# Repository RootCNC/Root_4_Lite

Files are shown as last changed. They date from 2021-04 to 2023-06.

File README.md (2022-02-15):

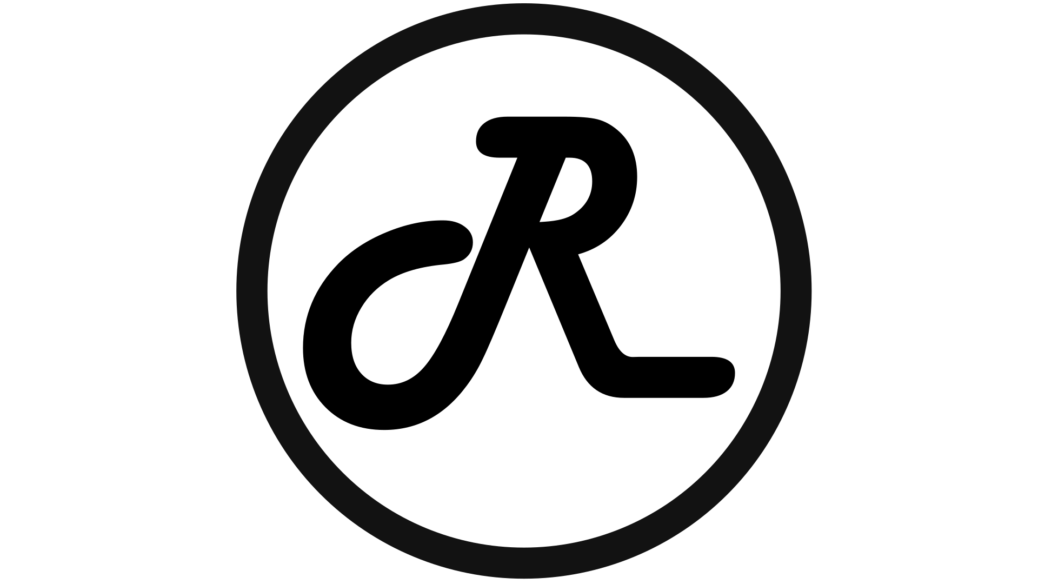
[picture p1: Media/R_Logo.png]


# Root 4 LITE CNC - High Performance small scale 3D Printed CNC Machine 

Root 4 Lite is deisgned to be a **low cost high performance CNC machine** that anyone can make at home.

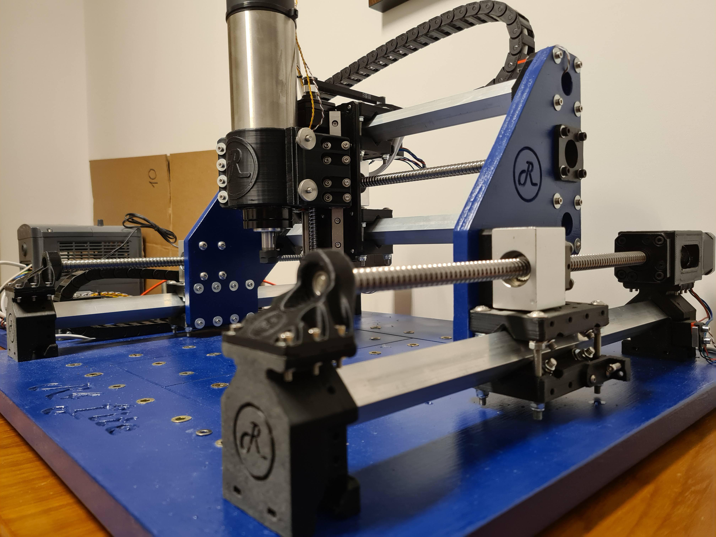
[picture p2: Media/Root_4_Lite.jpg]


### Goals
- Low Cost (Under £500)
- All bal screw design for percision movement
- Support for High performance VFD spindles
- Use low Cost NEMA17 Stepper motors
- Standard off the shelf parts
- Easily sourced components
- 3D printable
- Scaleable

## Spec
- Working Area = 224*280*60mm (Z,Y,Z) - Default build for other diemensions please see [LINK](https://github.com/RootCNC/Root_4_Lite/blob/main/Working%20Area.xlsx)
- Stepper Motor = NEMA 17 
- Aux rails for mounting a laser or dust shoe
- All ballscrew design
- Linear guide Z Axis
- Driect Drive Motors
- Full VFD support

## Videos

Youtube Videos can be found [Here](https://www.youtube.com/sailorpete12)

### Detailed build Videos

(http://www.youtube.com/watch?v=DjvXqU2bEzY "")

(http://www.youtube.com/watch?v=-5PmiW85Cyw "")

(http://www.youtube.com/watch?v=_y3V89cwmr8 "")

## License

This project is licensed under the Creative Commons 4.0 license with 
Attribution-NonCommerial-ShareAlike see `LICENSE.txt` for details

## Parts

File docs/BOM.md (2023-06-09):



# 3D Printed Parts required

|	3D Printed Parts  	|	Required	|	QTY	|	Total Weight (g)	|
|	---	|	---	|	---	|	---	|
|	Y_Axis_BoxMount.STL	|	4	|	YES	|	232g	|
|	Z_Y_Axis_BallscrewSpacer.STL	|	3	|	YES	|	39g	|
|	X_Axis_MotorMount.STL	|	1	|	YES	|	30g	|
|	X_Y_Axis_Carriage.STL	|	8	|	YES	|	344g	|
|	X_Axis_BearingIdler.STL	|	1	|	YES	|	17g	|
|	Y_Axis_Idler.STL	|	2	|	YES	|	28g	|
|	Z_Axis_Carriage_65mm.STL	|	1	|	YES	|	200g	|
|	Z_Axis_LinearRailMount.STL	|	1	|	YES	|	110g	|
|	Y_Aixs_DragChainMount.STL	|	1	|	YES	|	20g	|
|	X_Aixs_DragChainMount.STL	|	1	|	YES	|	15g	|
|	Z_Axis_MotorMount.STL	|	1	|	YES	|	40g	|
|	Y_Axis_Foot.STL	|	4	|	YES	|	32g	|
|	X_Axis_BoxMount.STL	|	2	|	YES	|	138g	|
|	DustShoe_Bottom.STL	|	1	|	YES	|	46g	|
|	DustShoe_Rail_Right.STL	|	1	|	YES	|	17g	|
|	DustShoe_Rail_Left.STL	|	1	|	YES	|	17g	|
|	Y_Axis_Motor_FK10_BearingMount.STL	|	2	|	YES	|	70g	|
|	Y_Axis_Endstop_Spacer.STL	|	1	|	NO	|	0g	|
|	Y_Axis_AdjEndstop.STL	|	1	|	NO	|	0g	|
|		|		|		|	Filament Used = 1395g	|

# Panels
| Item | QTY | Link|
|---|---|-----|
|Side_Panel|2|[Root CNC Store](https://rootcnc.com/product/root-4-lite-side-panels/)|
|Baseboard |1|Comming Soon|

# Electronics/ Electro Mechanical
| Item | Required | QTY | Link|
|---|---|---|-----|
|Root CNC ESP32-GRBL Controller |Yes|1|[LINK](https://rootcnc.com/product/root-controller-rev-2-1/)|
|Root CNC Controller Motor breakout (non-isolated) used DVR8825 or similar driver (Buy an isolated stepper driver) |Yes|1|Obsolete|
|DRV8825 or similar stepper motor drivers|Yes|4|[LINK](https://s.click.aliexpress.com/e/_A3iYCN) [LINK](https://s.click.aliexpress.com/e/_97wkVB) [UK LINK](https://amzn.to/3yf2EHw)
| Nema 17 Bipolar 59Ncm (84oz.in) 2A | Yes | 4 | [LINK](https://www.omc-stepperonline.com/nema-17-bipolar-59ncm-84oz-in-2a-42x48mm-4-wires-w-1m-cable-connector-17hs19-2004s1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) [LINK](https://www.omc-stepperonline.com/5pcs-of-nema-17-bipolaire-59ncm-84oz-in-2a-42x48mm-4-fils-w-1m-cable-connector-5-17hs19-2004s1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)
|1.5KW Spindle with VFD|Yes|1|[LINK_1](https://s.click.aliexpress.com/e/_dX0JKm3) [LINK_2](https://s.click.aliexpress.com/e/_dT4xs63) [LINK_3](https://s.click.aliexpress.com/e/_dSjt6gr) [LINK_4](https://s.click.aliexpress.com/e/_dSUhh43)
|Micro Switch SPDT micro switch V4 KW11i|Yes|6|[LINK UK](https://amzn.to/31Kf1wC) [LINK](https://s.click.aliexpress.com/e/_ATnQCz)| 
|12V or 24V PSU (For Controller power + any lights) |Yes|1|[12V_LINK_UK](https://amzn.to/2HxYvIS) [12V_lINK](https://s.click.aliexpress.com/e/_AACYyd)| 

# Motion
| Item | Required | QTY | Link|
|---|---|---|-----|
|608 Bearings | Yes | 4 |[LINK_UK](https://amzn.to/3dWB9c6), [LINK](https://s.click.aliexpress.com/e/_ATuujF)|
|625 Bearings | Yes | 38 |[LINK](https://s.click.aliexpress.com/e/_9iRVbr),  [LINK](https://s.click.aliexpress.com/e/_Ac5QYN),  [UK LINK](https://amzn.to/33OCsFN)|
|MGN12 150mm + (MGN12C x2) | Yes | 2 |[LINK](https://s.click.aliexpress.com/e/_A4Rr41)|
|GT2 Pulley 5mm Bore (16T) | Yes | 1 |[LINK](https://s.click.aliexpress.com/e/_9wTL2N),  [LINK](https://s.click.aliexpress.com/e/_9hLamt), [UK LINK](https://amzn.to/3waEtbq)|
|GT2 Pulley 8mm Bore (20T) | Yes | 1 |[LINK](https://s.click.aliexpress.com/e/_9wTL2N) |
|GT2 Closed loop belt (252 mm) | Yes |  1 ||
|Lead Screw 1204 400mm Long SFU1204 | Yes | 3 |[LINK](https://s.click.aliexpress.com/e/_9jDD3X),  [UK LINK](https://amzn.to/3eQJNLg)|
|Lead Screw 1204 200mm Long SFU1204 | Yes | 1 |[LINK](https://s.click.aliexpress.com/e/_Akbvnn), [UK LINK](https://amzn.to/3olI2sE)|
|Lead Screw ball nut Housing/Mount  SFU1204 | Yes |  3 |[LINK](https://s.click.aliexpress.com/e/_Ak3HhT), [UK LINK](https://amzn.to/3whPGqP)|
|FK10 Bearing Block | Yes |  4 |[LINK](https://s.click.aliexpress.com/e/_9RmTwd)|
|5mm to 8mm coupler | Yes | 3 |[LINK](https://s.click.aliexpress.com/e/_9AhiTb)  [UK LINK](https://amzn.to/3bwfNC8)|
|Drag Chain 10x20mm internal - 50cm | Yes |  2 |[LINK](https://s.click.aliexpress.com/e/_9wV1qz),  [UK LINK](https://amzn.to/3eURTm5)|

# Hardware
Below is guide on the QTY required/ the pack sizes I brought to assemble the Root 4 LITE CNC. I used Aluminium box section but steel would work just fine.
| Item | Required | QTY | Link|
|---|---|---|-----|
|20mm box section 410mm (scalable)|Yes|2||
|20mm box section 360mm (scalable)|Yes|2||

# Fixing List

|	Fixing list	|	Required	|	QTY	|
|	-----	|	-----	|	-----|
|	M3 PAN HEAD 20MM BOLT	|	Yes	|	30 (*1)	|
|	M3 PAN HEAD 25MM BOLT	|	Yes	|	30 (*1)	|
|	M3 PAN HEAD 30MM BOLT	|	Yes	|	30 (*1)	|
|	M3 CAP HEAD  10MM BOLT	|	Yes	|	30 (*1)	|
|	M3 CAP HEAD  14MM BOLT	|	Yes	|	30 (*1)	|
|	M3 CAP HEAD  16MM BOLT	|	Yes	|	30 (*1)	|
|	M3 CAP HEAD  25MM BOLT	|	Yes	|	30 (*1)	|
|	M3 CAP HEAD  30MM BOLT	|	Yes	|	30 (*1)	|
|	M3 NUTS	|	Yes	|	100 (*1)	|
|	M3 STANDARD WASHER	|	Yes	|	30 (*1)	|
|	M3 PENNY WASHER	|	Yes	|	50 (*1)	|
|	M4 CAP HEAD 25MM BOLT	|	Yes	|	30 (*1)	|
|	M4 CAP HEAD 40MM BOLT	|	Yes	|	30 (*1)	|
|	M4 NUTS	|	Yes	|	50 (*1)	|
|	M4 STANDARD WASHERS	|	Yes	|	50 (*1)	|
|	M5 HEX HEAD 20MM BOLT	|	Yes	|	32	|
|	M5 PAN HEAD 20MM BOLT	|	Yes	|	20 (*1)	|
|	M5 PAN HEAD 30MM BOLT	|	Yes	|	20 (*1)	|
|	M5 PAN HEAD 60MM BOLT	|	Yes	|	16	|
|	M5 WASHERS	|	Yes	|	128	|
|	M5 NUTS	|	Yes	|	100 (*1)	|
|	M5 LOC NUTS	|	Yes	|	100  (*1)	|
|	M5 KNURLED THUMB NUTS 	|	Yes	|	4	|
|	M6 INSERTS NUTS	|	Yes	|	42	|

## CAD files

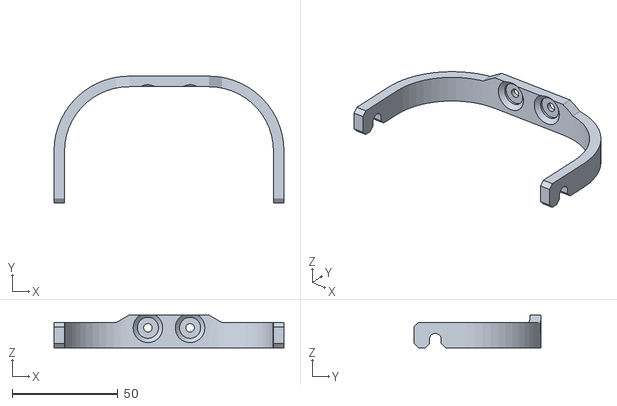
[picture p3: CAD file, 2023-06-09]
Addons/Laser Mount (LT-80W-AA)/Z_AxisMountBottom.stl
109.0 x 60.0 x 15.5

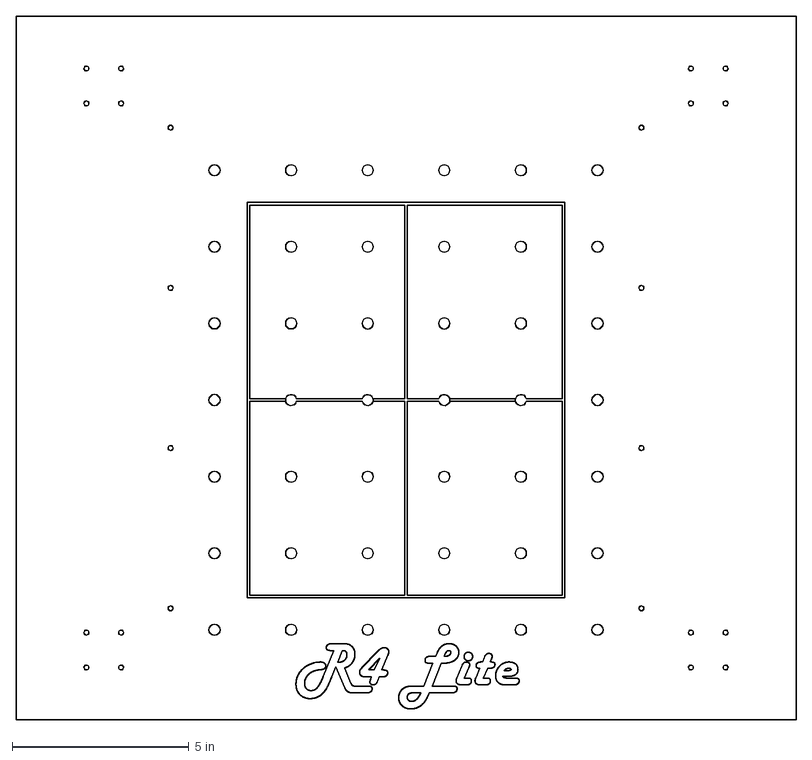
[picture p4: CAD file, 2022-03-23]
Source/DXF_Files/Root_4_Base_Board.dxf
22.0 x 19.9 in

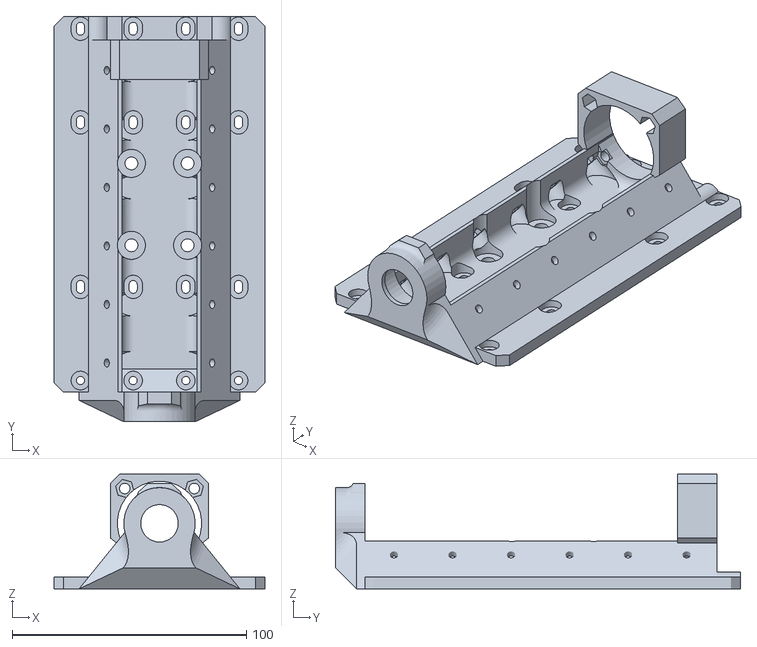
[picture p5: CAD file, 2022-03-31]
Source/STL_Files/Z_Axis_LinearRailMount.STL
90.0 x 173.0 x 49.0

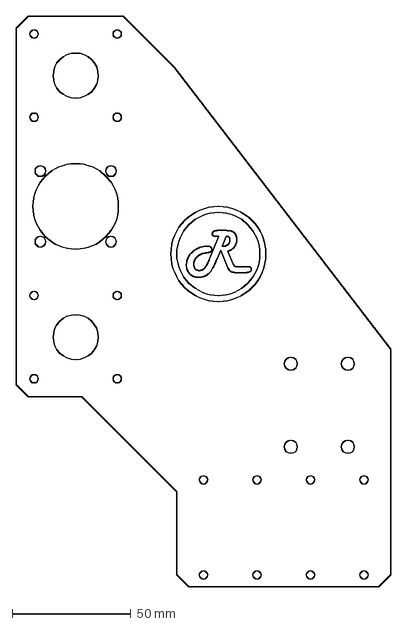
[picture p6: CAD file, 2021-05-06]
Source/DXF_Files/Root_4_Lite_Side_Panel_(Front).DXF
157.5 x 240.0 mm

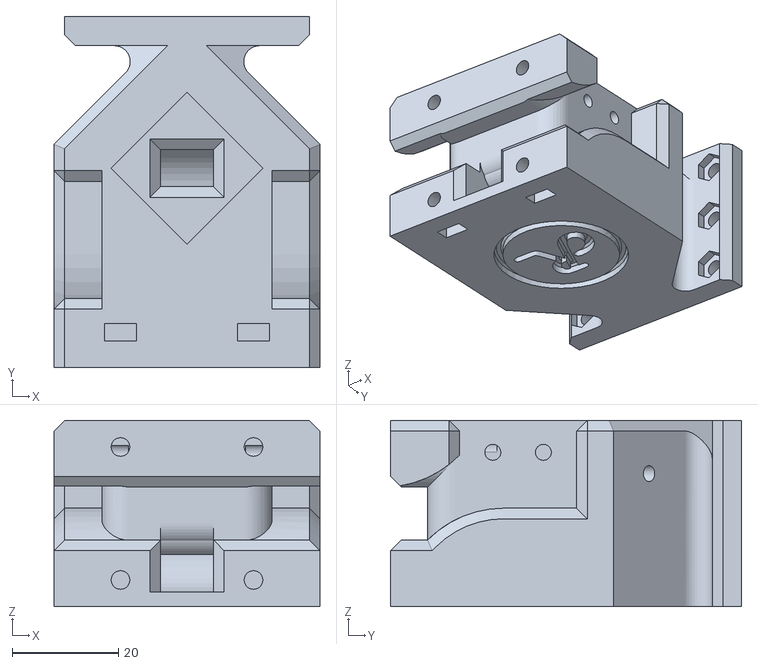
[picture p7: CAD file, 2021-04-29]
Source/STL_Files/Y_Axis_BoxMount.STL
50.0 x 66.0 x 35.0

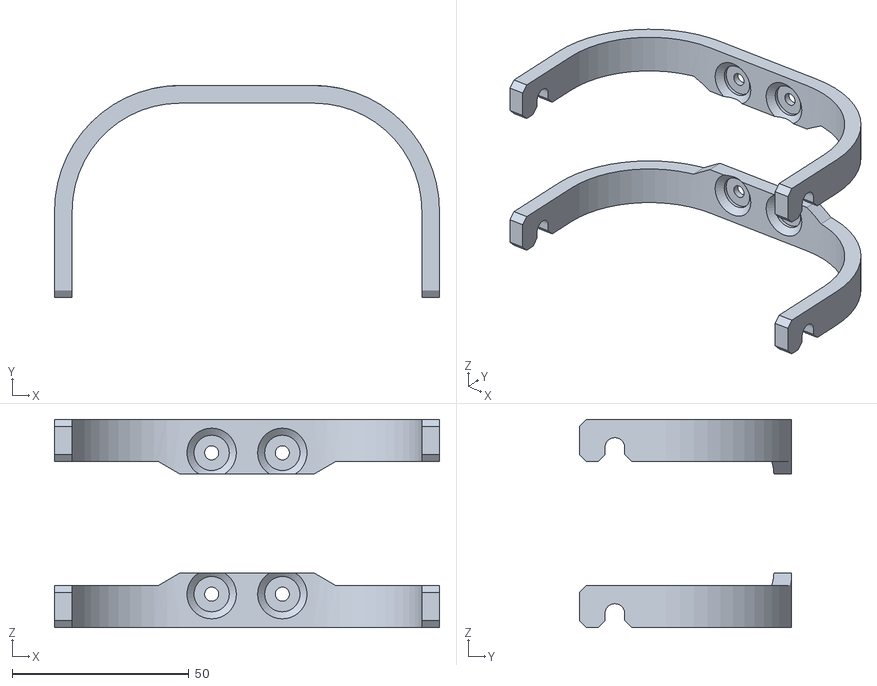
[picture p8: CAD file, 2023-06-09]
Addons/Laser Mount (LT-80W-AA)/Z_AxisMount.STL
109.0 x 60.0 x 59.0

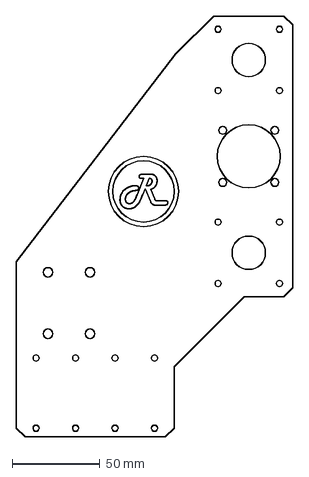
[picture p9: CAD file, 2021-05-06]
Source/DXF_Files/Root_4_Lite_Side_Panel_(Back).DXF
157.5 x 240.0 mm

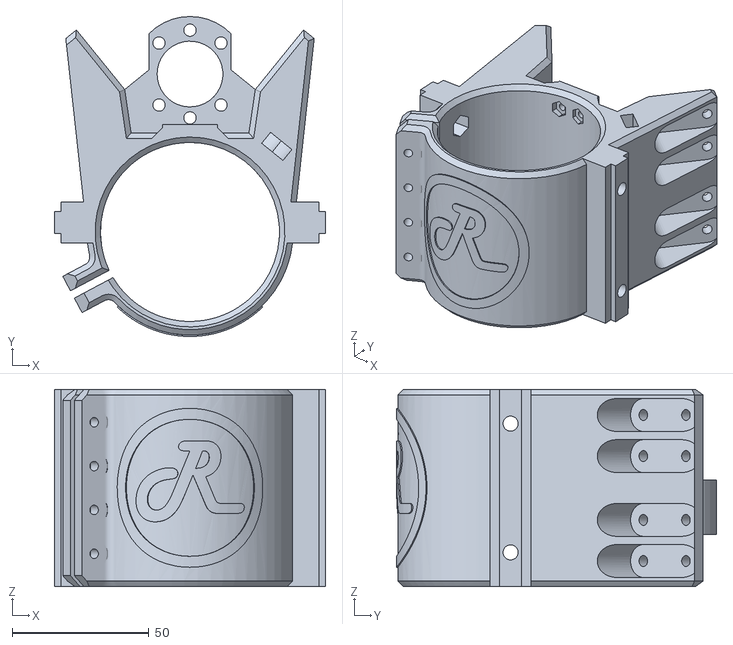
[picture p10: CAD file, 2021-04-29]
Source/STL_Files/Z_Axis_Carriage_65mm.STL
99.0 x 116.8 x 72.0

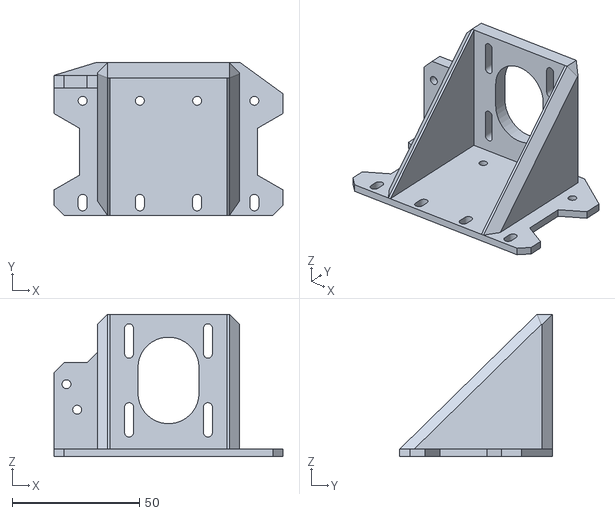
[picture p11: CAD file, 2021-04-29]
Source/STL_Files/Z_Axis_MotorMount.STL
90.0 x 60.0 x 56.0

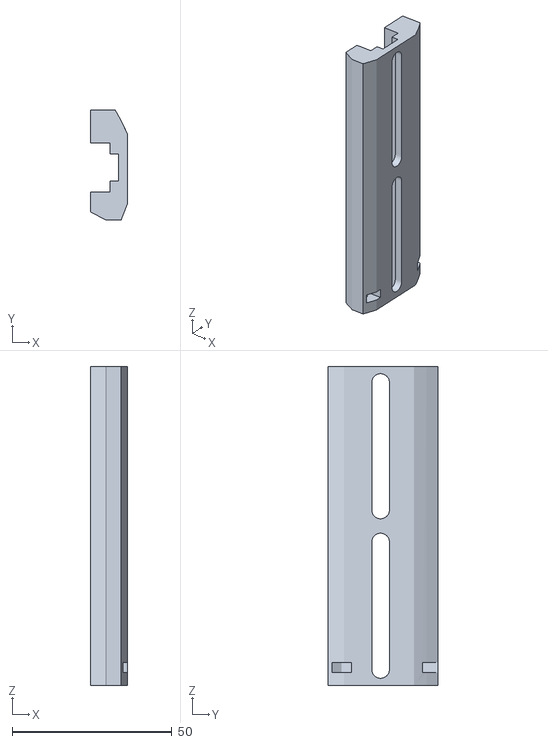
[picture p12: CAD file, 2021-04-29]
Source/STL_Files/DustShoe_Rail_Right.STL
11.5 x 34.5 x 100.0

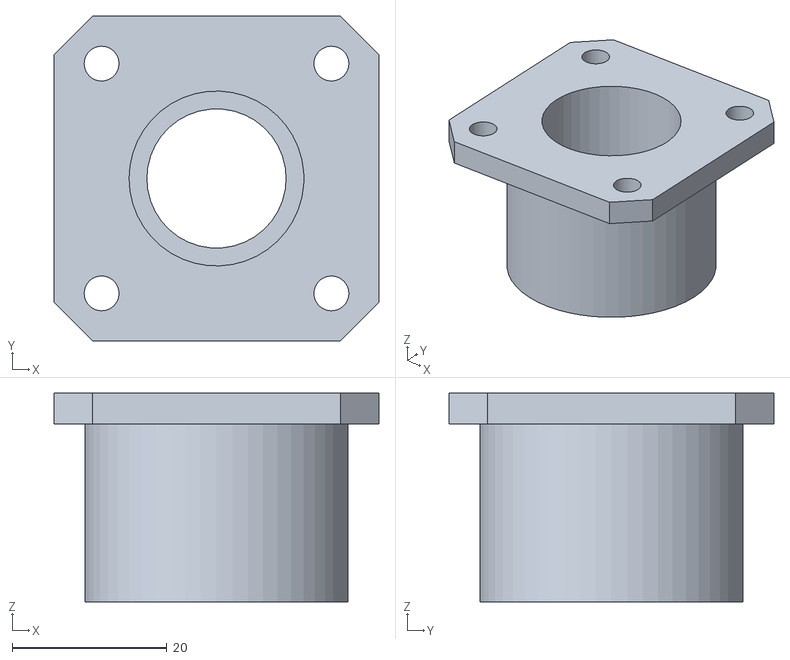
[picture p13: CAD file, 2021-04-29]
Source/STL_Files/X_Axis_BearingIdler.STL
42.0 x 42.0 x 27.0

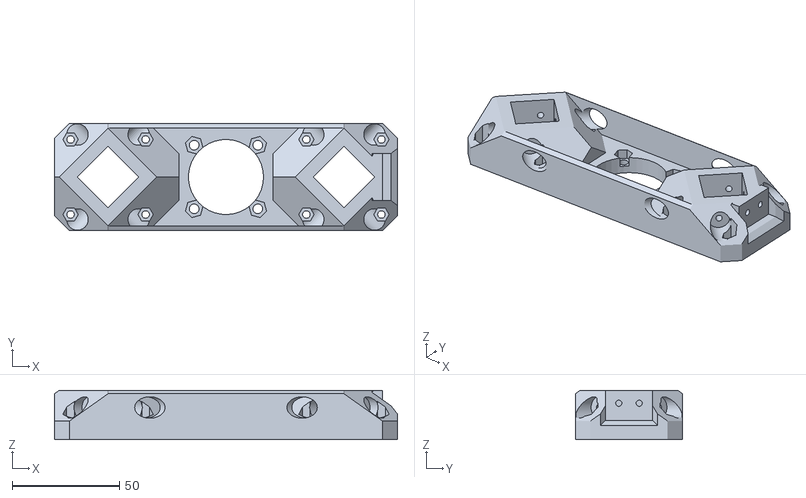
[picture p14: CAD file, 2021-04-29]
Source/STL_Files/X_Axis_BoxMount.STL
160.0 x 50.0 x 23.0

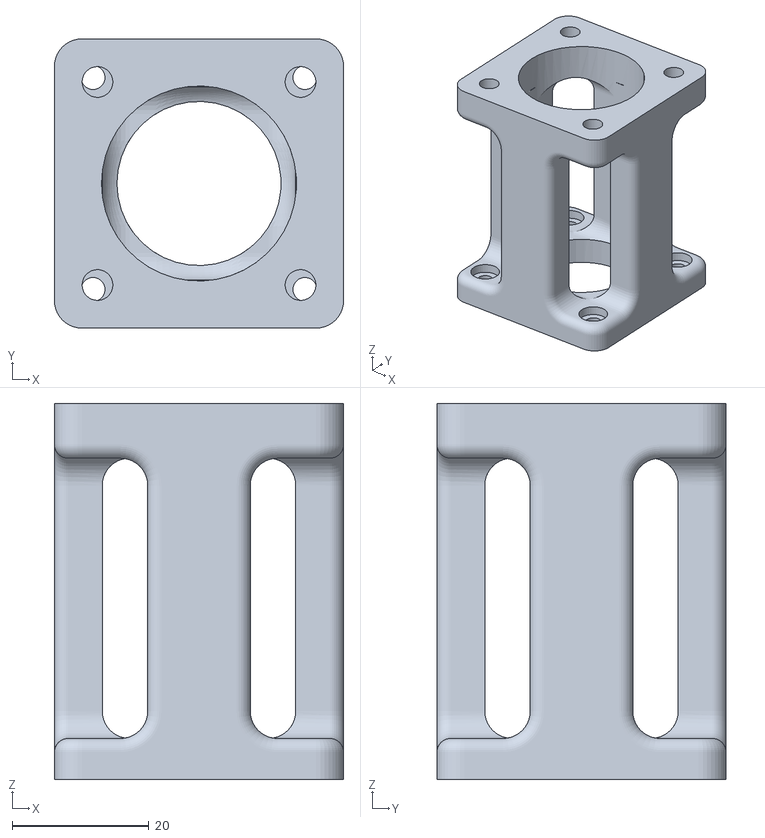
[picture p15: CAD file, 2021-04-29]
Source/STL_Files/X_Axis_MotorMount.STL
42.3 x 42.3 x 55.0

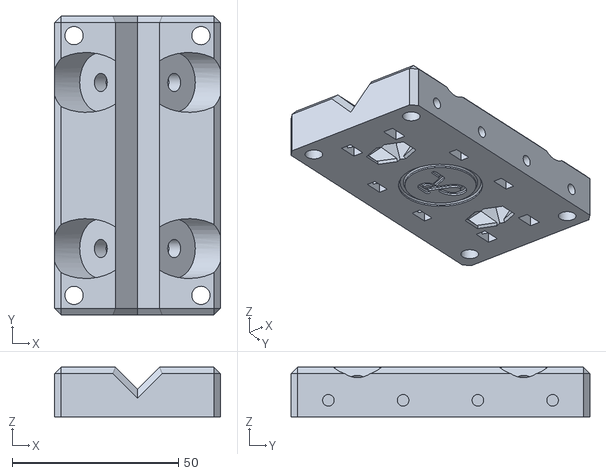
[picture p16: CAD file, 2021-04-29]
Source/STL_Files/X_Y_Axis_Carriage.STL
50.0 x 90.0 x 15.0

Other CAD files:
Addons/Laser Mount (LT-80W-AA)/Z_AxisMountTop.stl
Source/STL_Files/Y_Axis_Foot.STL
Source/STL_Files/Y_Axis_Idler.STL
Source/STL_Files/DustShoe_Bottom.STL
Source/STL_Files/X_Aixs_DragChainMount.STL
Source/STL_Files/Y_Aixs_DragChainMount.STL
Source/STL_Files/Y_Axis_AdjEndstop.STL
Source/STL_Files/Y_Axis_Endstop_Spacer.STL
Source/STL_Files/Y_Axis_Motor_FK10_BearingMount.STL
Source/STL_Files/Z_Y_Axis_BallscrewSpacer.STL

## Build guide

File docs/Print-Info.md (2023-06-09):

---
title: Root 4 Lite Print Orientation
description: How to print the parts for the Root 4 Lite
published: true
date: 2022-06-28T22:24:57.245Z
tags: root 4 lite, how to print
editor: markdown
dateCreated: 2022-06-28T22:17:17.168Z
---

# How to Print
Print settings for any of the Root CNC machine is key for a long lasting - high performance CNC machine. Below are the setting I used:

Resolution: 0.25-0.35mm
Infill: 50-60%
## Notes:
- Strength is key! use the hardest settings possible
- Print with 3-4 perimeters
- Print with ABS, PETG PLA will be fine though your mileage may vary (I am worried about the low glass transistion point of PLA being too low for the motors)

# DustShoe_Bottom.STL

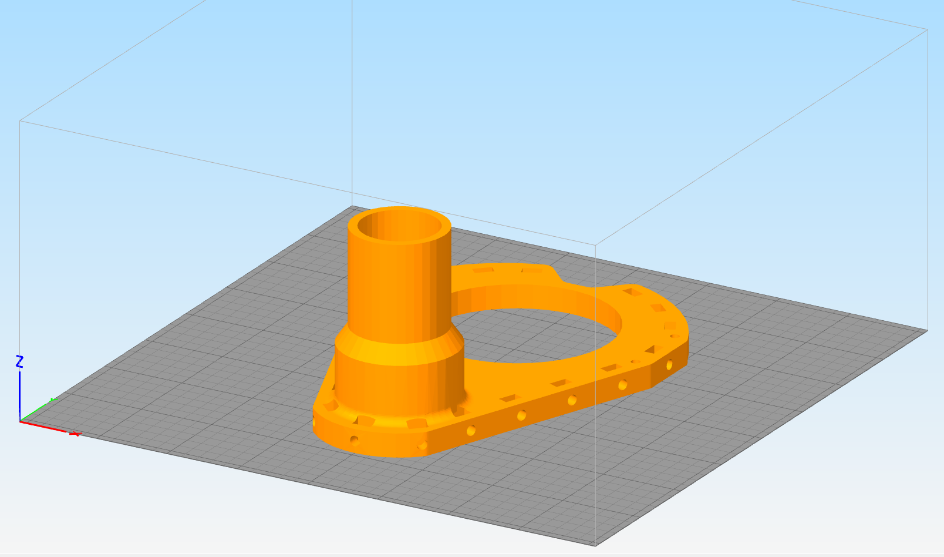
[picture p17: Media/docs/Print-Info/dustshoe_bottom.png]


# DustShoe_Rail_Right.STL

> For the left side - Please mirror in your slicer
{.is-info}

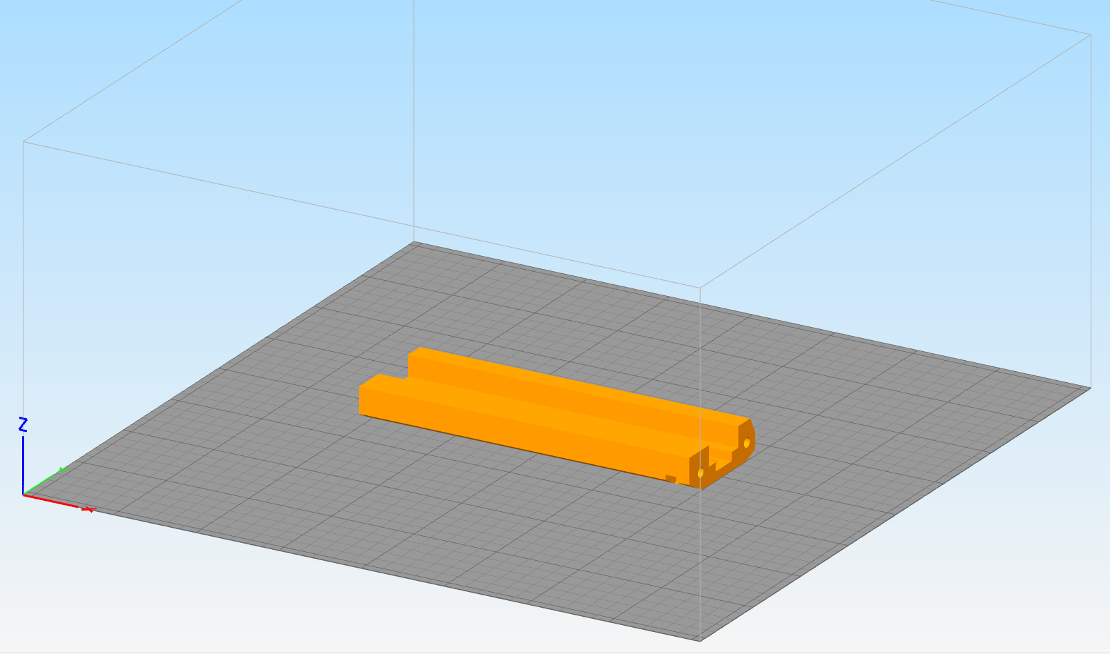
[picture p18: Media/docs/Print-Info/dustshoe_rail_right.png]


# X_Aixs_DragChainMount.STL.
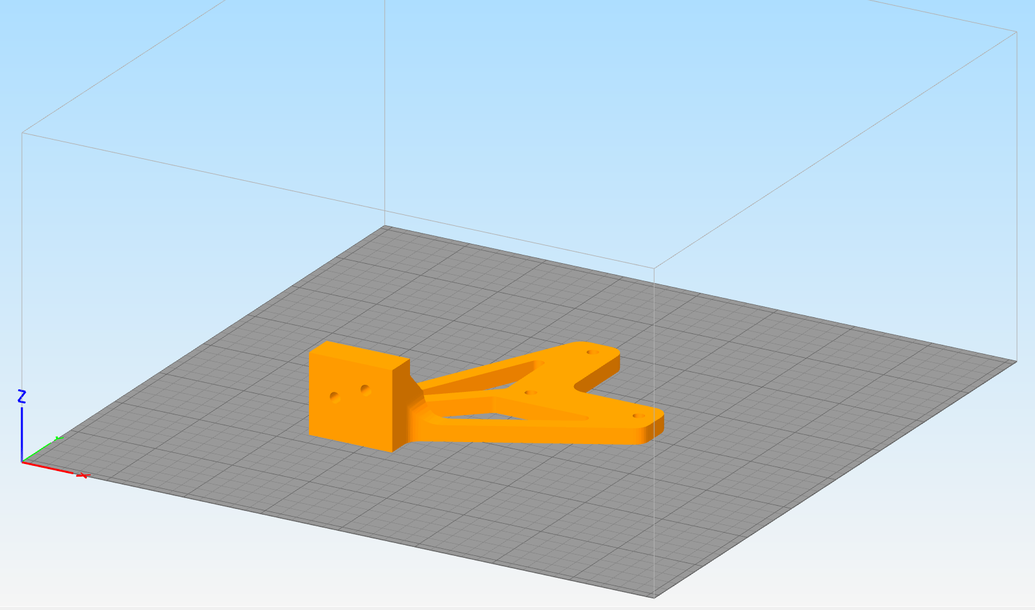
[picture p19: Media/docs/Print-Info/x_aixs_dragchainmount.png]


# X_Axis_BearingIdler.STL
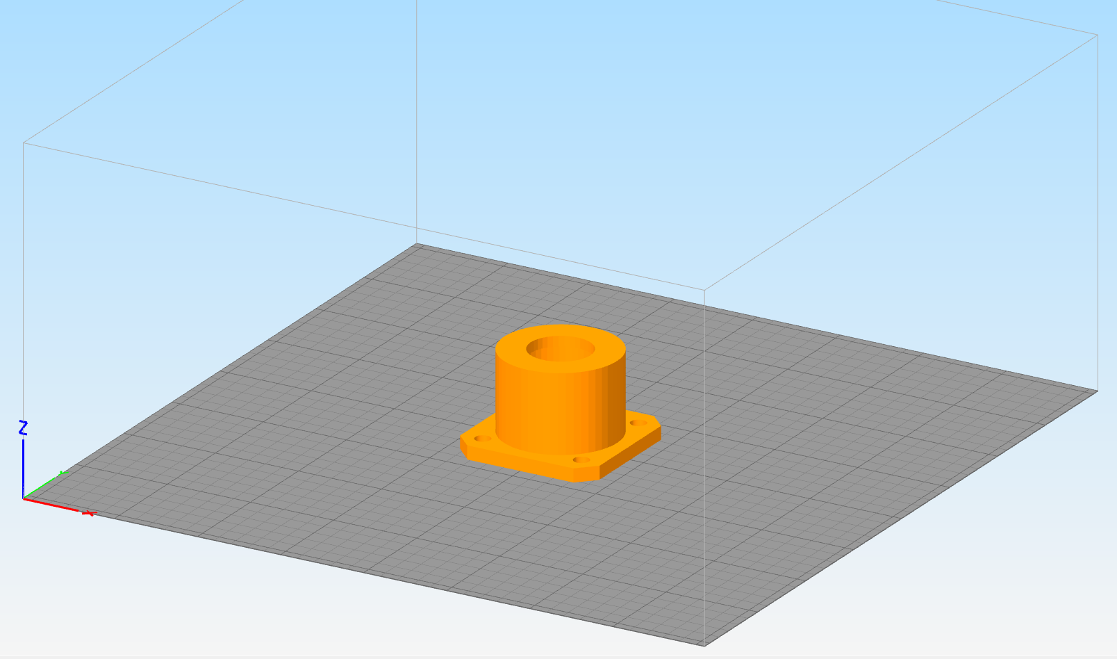
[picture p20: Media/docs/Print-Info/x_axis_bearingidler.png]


# X_Axis_BoxMount.STL
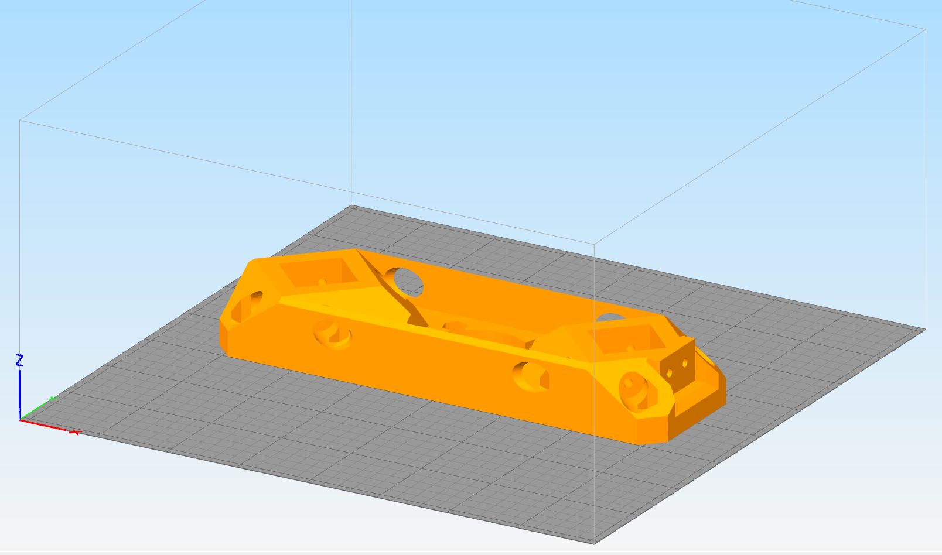
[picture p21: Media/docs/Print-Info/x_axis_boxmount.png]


# X_Axis_MotorMount.STL

> Needs supports, print with hex nut end down

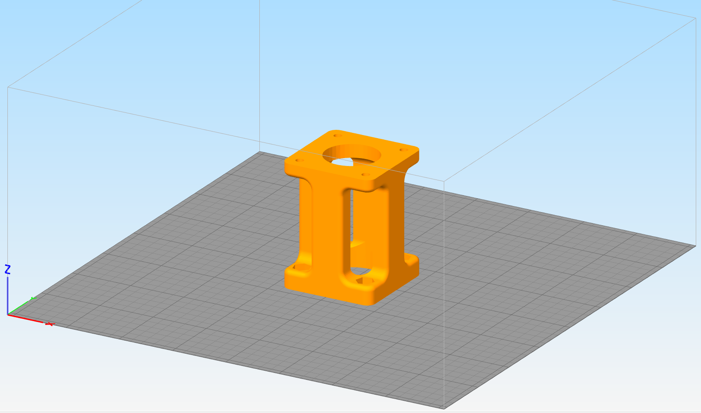
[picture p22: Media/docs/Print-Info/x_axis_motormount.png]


# X_Y_Axis_Carriage.STL
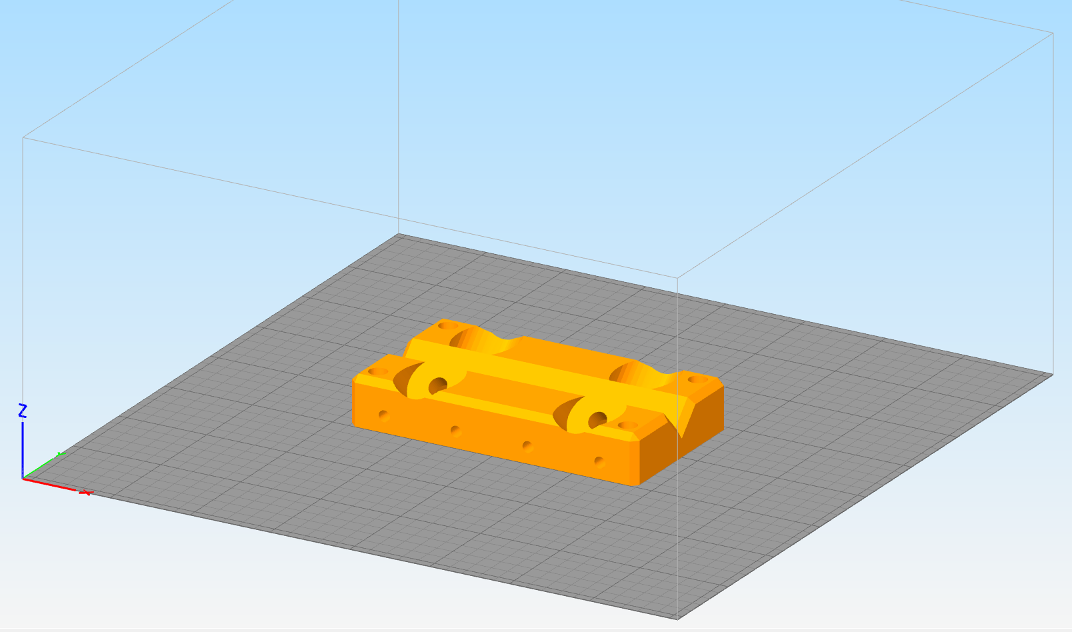
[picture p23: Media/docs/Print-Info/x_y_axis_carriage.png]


# Y_Aixs_DragChainMount.STL
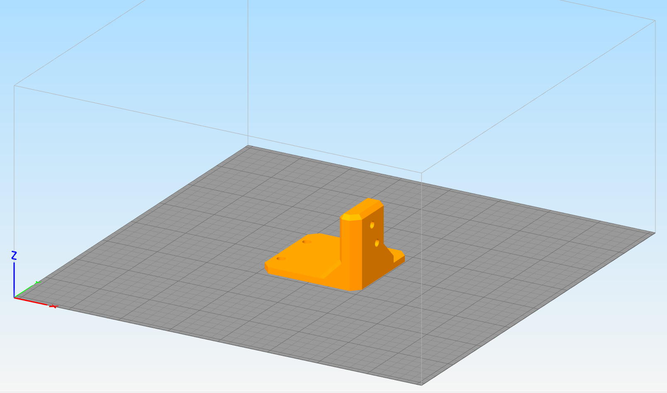
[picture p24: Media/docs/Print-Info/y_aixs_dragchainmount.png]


# Y_Axis_BoxMount.STL
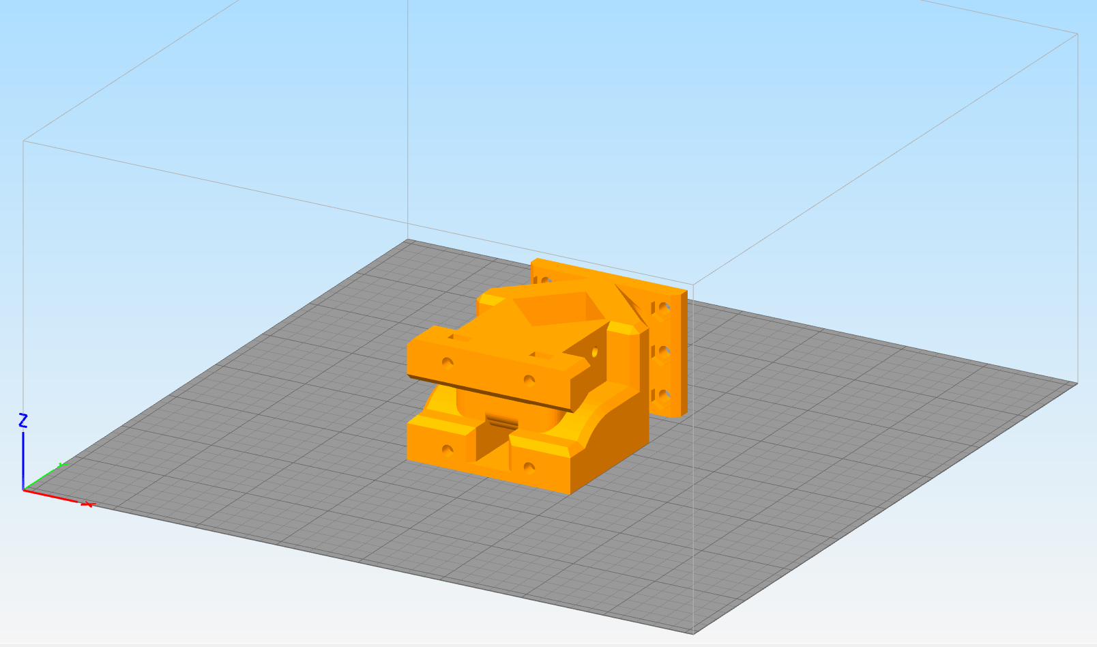
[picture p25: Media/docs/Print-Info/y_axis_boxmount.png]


This piece needs some support, you can paint it like this (you need it only for the leg, everything else prints just fine without support):

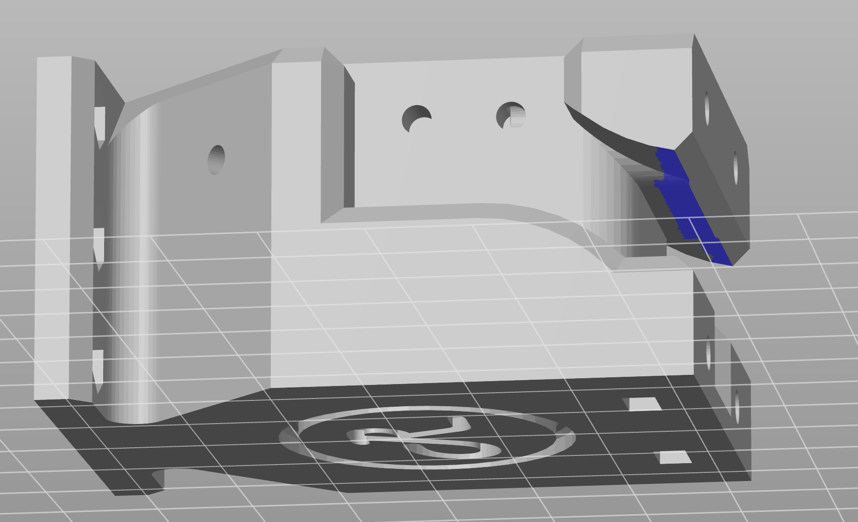
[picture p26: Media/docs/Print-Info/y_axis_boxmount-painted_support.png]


Here's how the support will look like. It will be easy to remove and it's on internal faces, so it will not be visible once mounted.

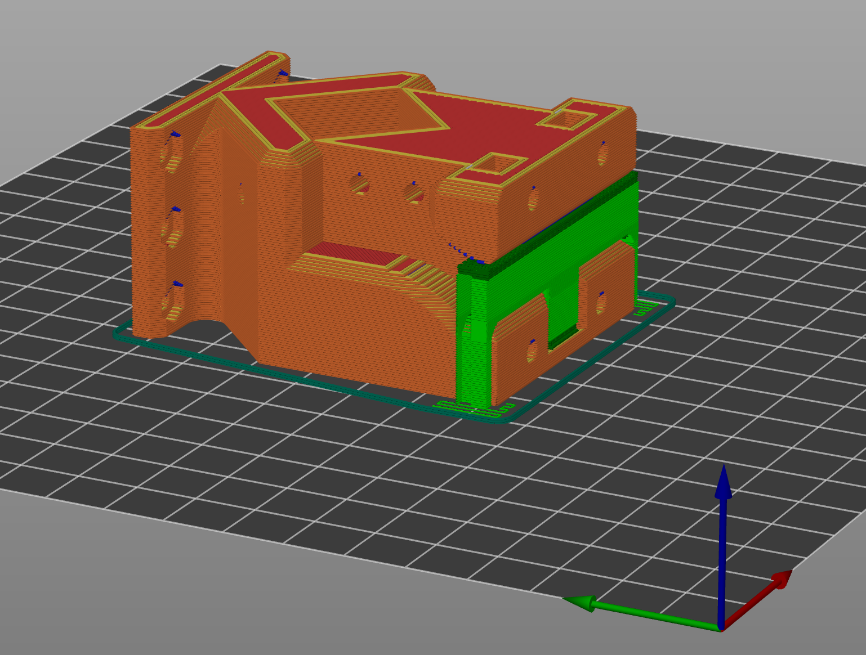
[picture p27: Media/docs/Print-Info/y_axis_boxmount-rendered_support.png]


# Y_Axis_Foot.STL
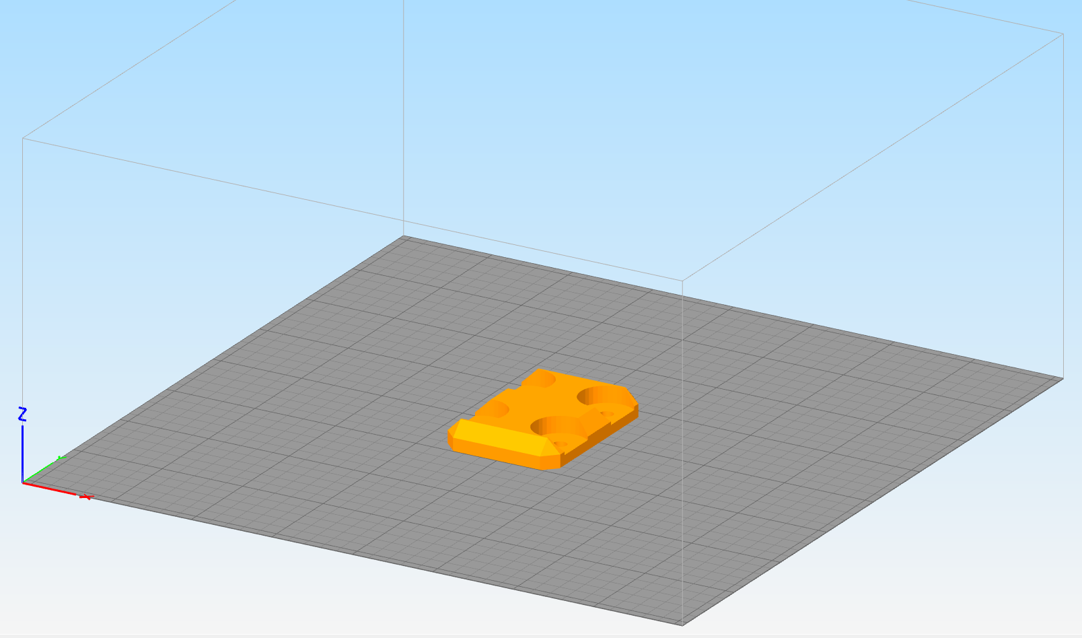
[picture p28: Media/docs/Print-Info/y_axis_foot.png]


# Y_Axis_Idler.STL
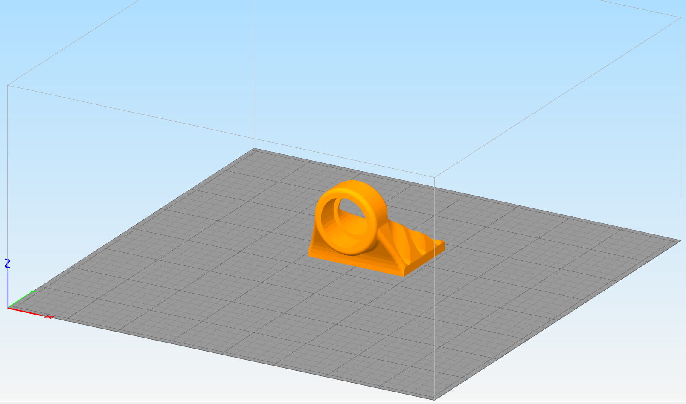
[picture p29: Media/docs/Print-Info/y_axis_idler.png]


This piece needs a little support, you can paint it like this:

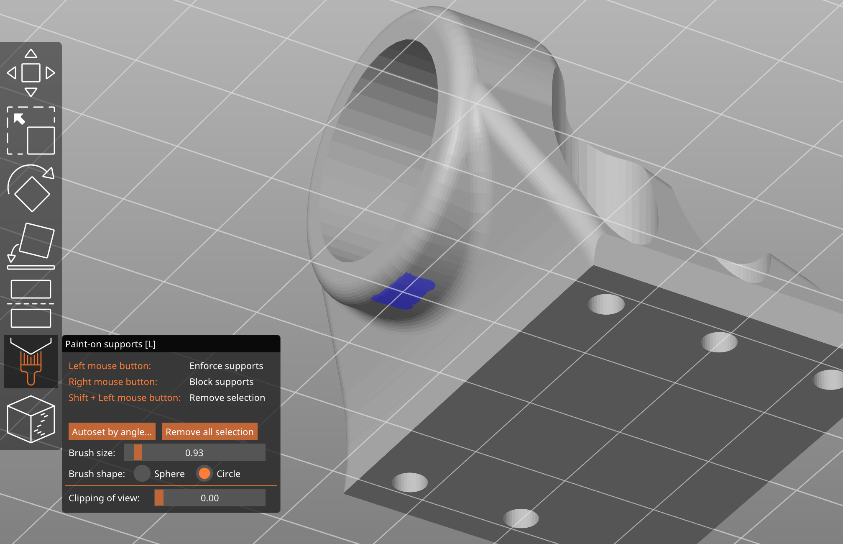
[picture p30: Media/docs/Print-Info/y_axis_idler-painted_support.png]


Here's how the support will look like. It will be easy to remove and it's on a down facing spot, so it will not be visible once mounted.

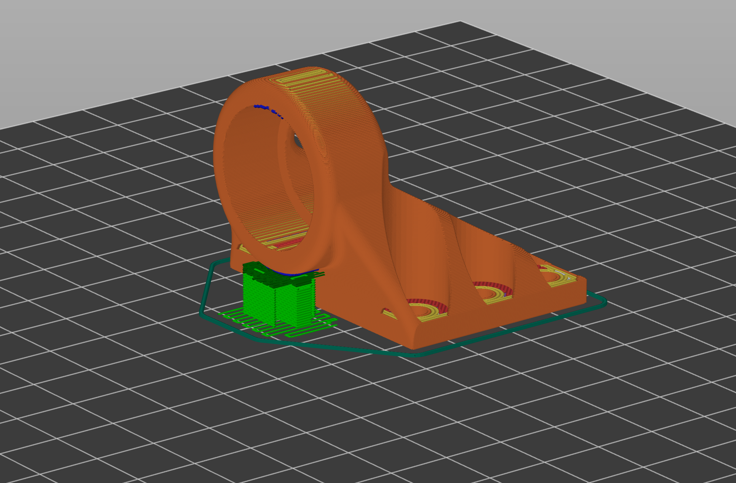
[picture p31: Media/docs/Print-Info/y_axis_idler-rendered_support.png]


# Y_Axis_Motor_FK10_BearingMount.STL
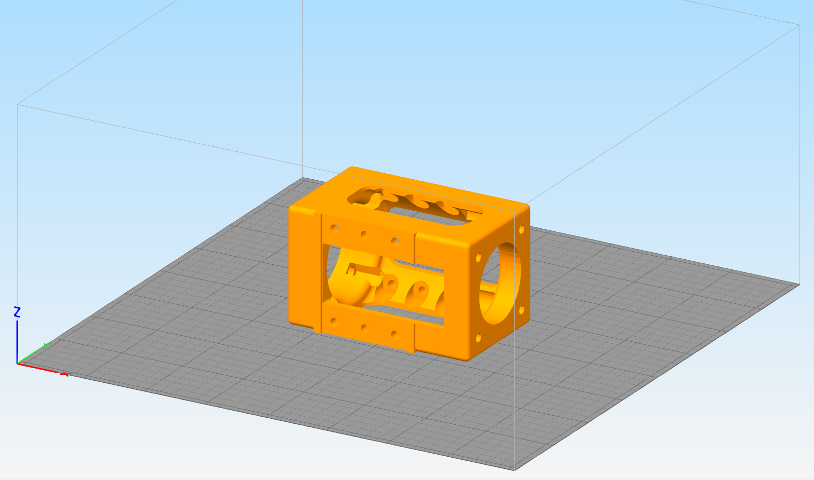
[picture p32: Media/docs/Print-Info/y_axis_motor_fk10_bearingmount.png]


This part needs some support for both the long bridges and the hex bolt point. I (Valerioa) forgot to add support on the hex bolt overhang and got a big blob (the part will be probably usable, but a bit support should result in a better print)

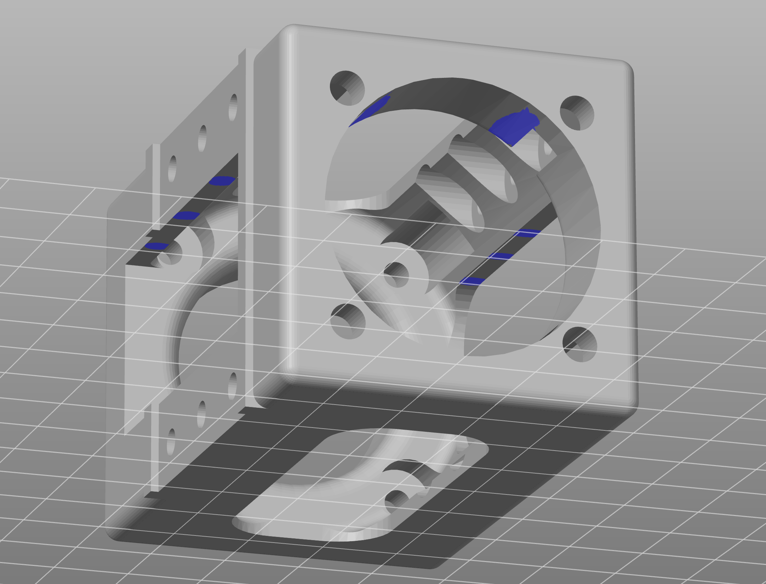
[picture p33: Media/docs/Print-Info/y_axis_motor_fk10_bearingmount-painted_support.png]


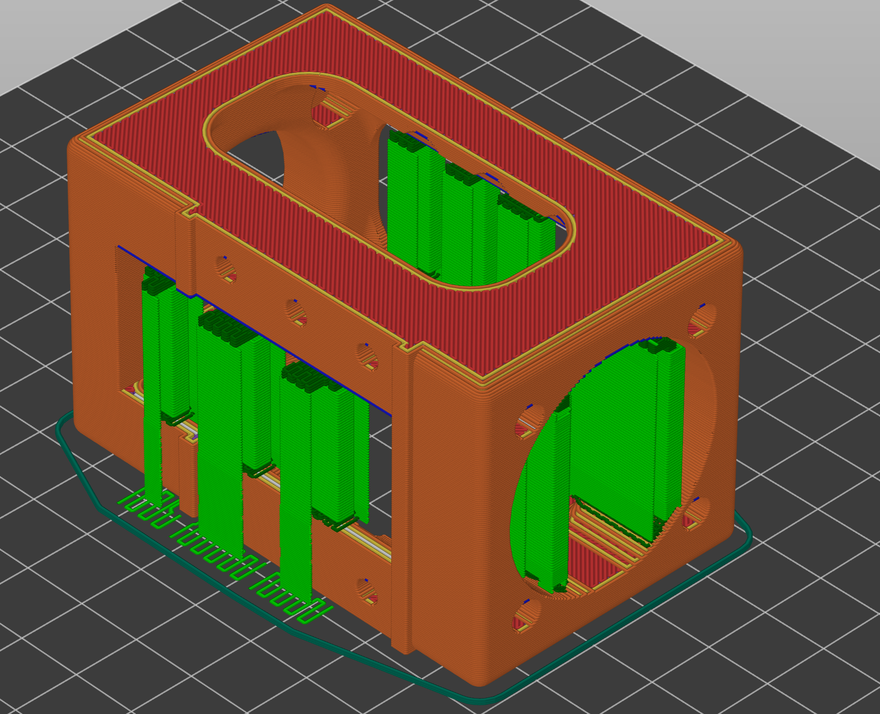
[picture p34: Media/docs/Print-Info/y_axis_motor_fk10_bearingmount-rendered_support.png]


# Z_Axis_Carriage_65mm.STL
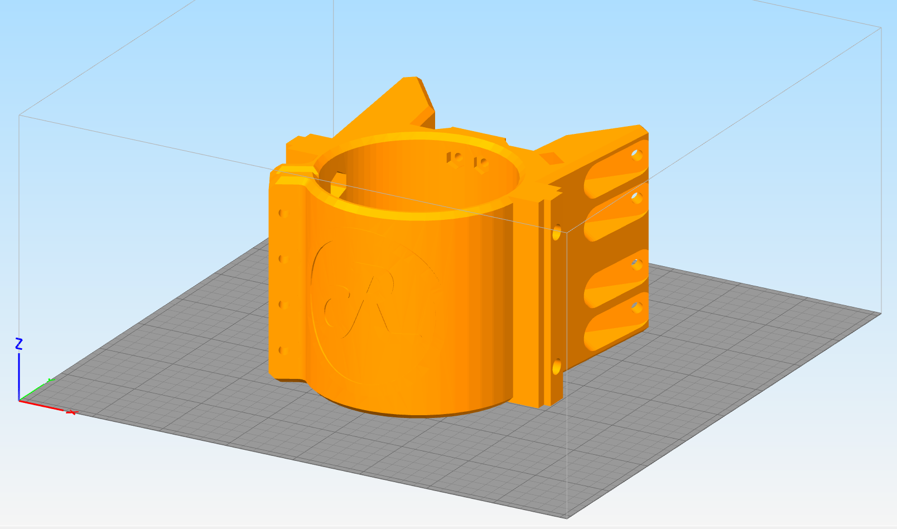
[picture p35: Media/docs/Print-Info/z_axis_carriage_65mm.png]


This is probably one of the biggest, heaviest and longest prints for this project, so you definitely want to get it right on the first print.
You'll need support for the entire bottom face of the ballscrew bolt mount. To preserve your sanity, add the support only on the bottom face, without going into the bolt's holes. Going into the bolt's holes is not necessary and the support will be a pain to remove, with the risk of damaging the hole's shape.
Here's quoted a post from RobF from the discord channel talking about this piece:
"The bottom face and holes on my primitive printer were a bit "grotty", but it doesn't matter as you only need to be able to get your hex nuts into those 6 holes and the bolts above will pull them up into the recess and crush any little bits of support you missed.  Its all facing down and hidden at the back of the carriage so no-one will see it. I was initially a bit concerned how structurally sound it would all come out, but the Z axis assembly and strong bolts ensures its all rock solid in the end."

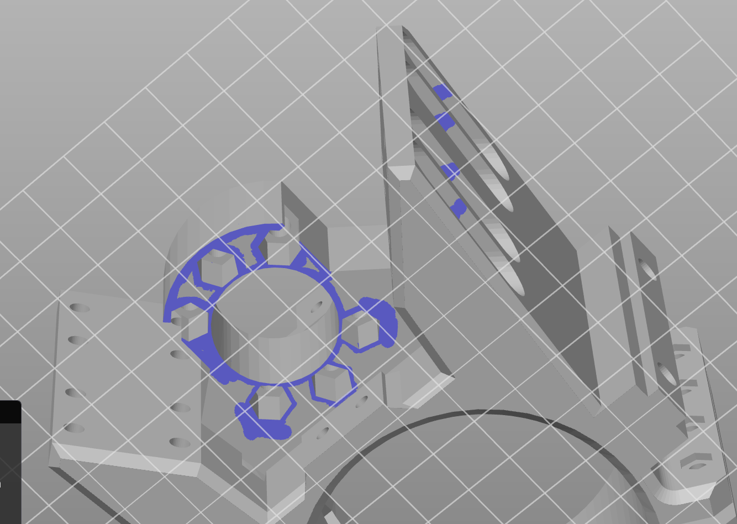
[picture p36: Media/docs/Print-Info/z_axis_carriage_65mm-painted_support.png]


Here's how it will look like. Small supports can be added to support the bridging on the sides. They should print fine without supports if your printer is well tuned for bridging, but on a 10+ hours print it's marginal in terms of both print time and wasted material, so better safe than sorry.

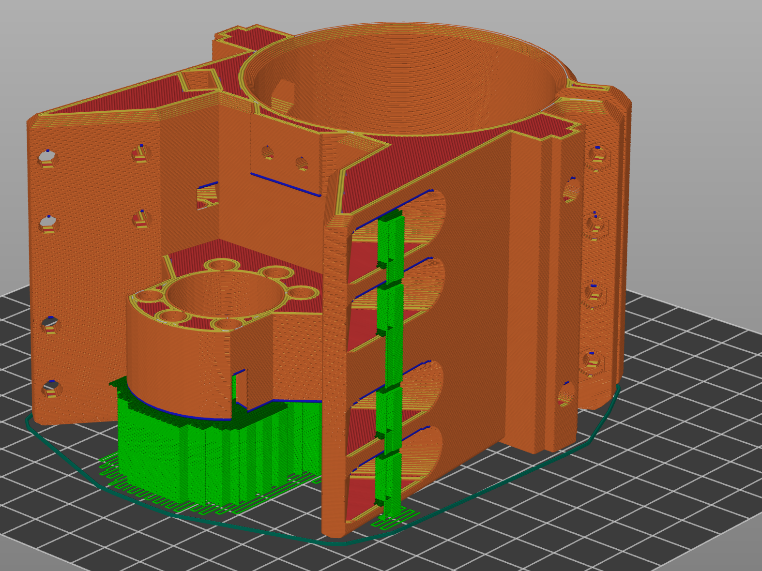
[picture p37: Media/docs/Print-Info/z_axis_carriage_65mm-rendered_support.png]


# Z_Axis_LinearRailMount.STL
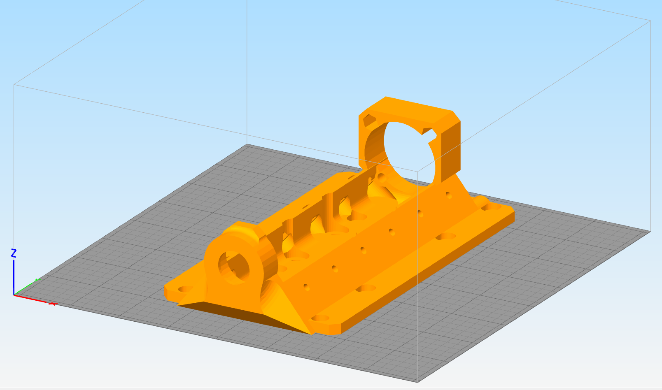
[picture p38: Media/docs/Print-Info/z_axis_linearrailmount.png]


# Z_Axis_MotorMount.STL
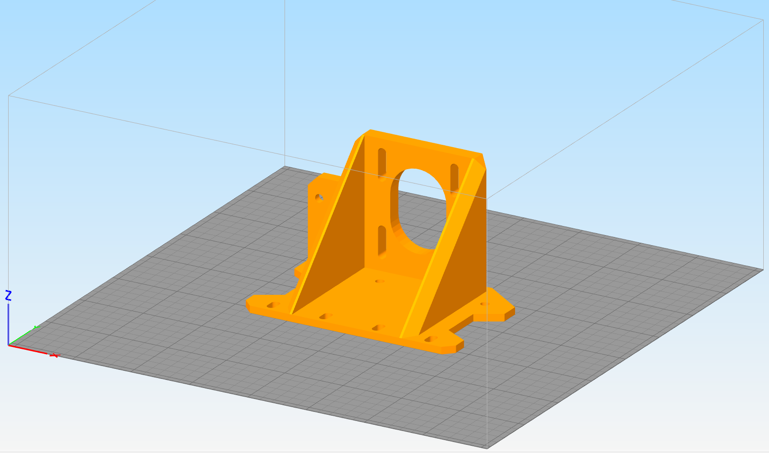
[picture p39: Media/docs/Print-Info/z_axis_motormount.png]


# Z_Y_Axis_BallscrewSpacer.STL
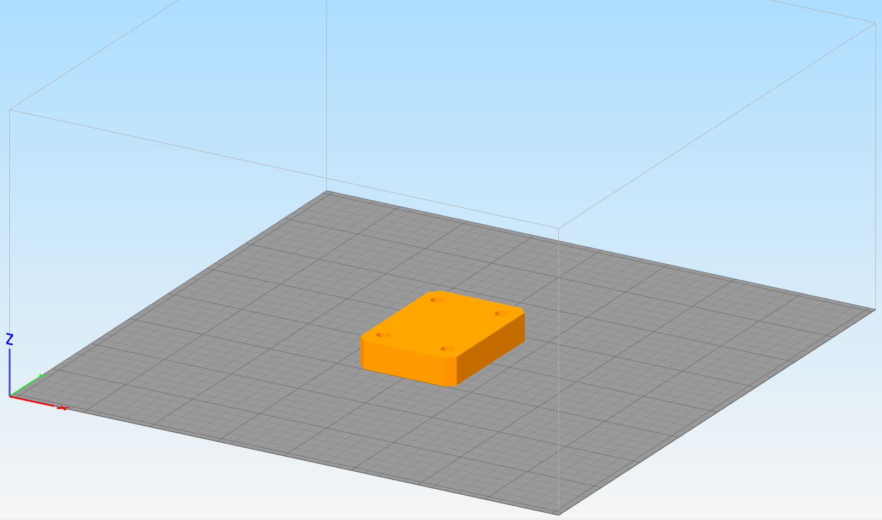
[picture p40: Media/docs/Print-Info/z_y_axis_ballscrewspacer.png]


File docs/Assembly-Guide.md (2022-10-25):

---
title: Root 4 Lite Assembly Guide
description: Root 4 Lite Assembly Guide for Newbies
published: true
date: 2022-06-28T21:37:30.411Z
tags: root 4 lite, r4 lite, guide
editor: markdown
dateCreated: 2022-05-24T19:30:47.756Z
---

# Root 4 Lite Assembly Guide for Newbies
> Please note: This Assembly guide was community made by #RobF - please send your love his way!
>
> If you would like to support the project in any shape or form, please get in touch with Pete! 
{.is-success}

# Introduction
So, you’ve watched all [Pete’s YouTube videos](https://www.youtube.com/c/sailorpete12/videos), admired the elegant simplicity of the Root 4 Lite (R4L) design.  You’ve compared the costs of buying a Chinese 3018 engraver or other DIY CNCs and can see a strength, performance, simplicity benefit in the Root CNCs.  You’ve got access to a 3D printer and may have even started printing Root CNC parts.  The only problem is you’ve never built a CNC or operated one before.  Fear not, others have been this way and succeeded with some planning and patience.  

This guide aims to provide a bit more detail on how to plan, print, build, and check basic operation of our R4L CNC.  

# Resources
Root 4 Lite Github: [Link Here](https://github.com/RootCNC/Root_4_Lite)
## Useful Links
- Bill of Materials (BOM): [Link here](https://github.com/RootCNC/Root_4_Lite/tree/main/BOM)
- Source STL and DXF Files: [Link here](https://github.com/RootCNC/Root_4_Lite/tree/main/Source)
- Working Area spreadsheet calculator: [Working%20Area.xlsx](https://github.com/RootCNC/Root_4_Lite/blob/main/Working%20Area.xlsx)

## Useful Videos
YouTube – make sure you’re familiar with the 4 R4L assembly videos:
- [Another 3D Printed CNC Machine? PT1](https://www.youtube.com/watch?v=DjvXqU2bEzY)
- [Building a small High performance 3D printed CNC machine – Root 4 Lite PT2](https://www.youtube.com/watch?v=-5PmiW85Cyw&t=618s)
- [3D Printed CNC Machine – Root 4 Lite PT3](https://www.youtube.com/watch?v=_y3V89cwmr8)
- [Root 4 Lite PT4 – the final stage assembly for the DIY 3D printed CNC machine](https://www.youtube.com/watch?v=ivuQiyucW90&t=402s)

## Social links
- [Root 4 Lite CNC Webpage](https://rootcnc.com/root-4-lite/)
- [Facebook Group](https://www.facebook.com/groups/rootcnc/)
- [Discourse](https://rootcnc.discourse.group/)
- [Root CNC Discord Channel](https://discord.gg/93Ue5SwthW) Great for quick answer to questions
- [Thingiverse](https://www.thingiverse.com/sailorpete/designs)
- [Youtube](https://www.youtube.com/c/sailorpete12/)

# Planning and Preparation
## Practicalities
Where is your machine going to live, and can your significant other or neighbours cope with the noise and dust?  How much space do you realistically have available.  What materials do you expect to be cutting?  The Root 4 Lite is a great compromise between relatively easy to understand parts, few special tools, strong design, and flexible sizing options.

The majority of 3D parts are not overly complex, show thoughtful design to avoid weak points, and will fit on the baseplate of a modest 3D printer (200x200mm).  

## 3D printed parts
These need to be dimensionally precise – check your printer is calibrated and capable of reproducing parts to correct sizing.  Consider printing a 20mm [calibration cube](https://www.thingiverse.com/thing:1278865).  Aim to print with more walls than usual (e.g. 3-6), higher % infill.  Layer sizes of 0.3 – 0.4 mm printed in PLA, PLA+, or ABS should all be fine.  Where supports are required be prepared to remove as much of this as possible later.  Most parts contain cavities or indentations for receiving bolts and nuts – check these spots are particularly clean before assembly begins.

## Sizing
Use the excellent [sizing spreadsheet](https://github.com/RootCNC/Root_4_Lite/blob/main/Working%20Area.xlsx) from the Github site.  Bigger is not always better – for ballscrew sizes approaching 750-1000mm, consider building a full [Root 4 CNC](https://rootcnc.com/root-4/) for a stronger, more capable (and more expensive) machine.  The spreadsheet assumes you will be using 12mm thick side panels.  Warning:  If you use thicker or thinner material, the size of your X axis ballscrews and Box Section Lengths may need adjustment.  

The R4L side panels contain main important mounting holes for the Y axis carriages and X axis assemblies.  It is highly recommended you consider purchasing these from the Root CNC website shop, or have them made up locally (from the BOM DXF files section).  If possible avoid attempting to cut them manually – it will make your building significantly easier.

The [Github](https://github.com/RootCNC/Root_4_Lite) site also includes a DXF file for preparing a suitable 18mm baseboard with holes positions for mounting Y Axis supports and threaded inserts.

## Choice of Spindle/Router
Pete has designed the R4L specifically for a cooled 240V spindle driven by a VFD.  This should result in optimal control over spindle speed, cutting power, noise and longevity.  It is also possible to fit a 240V/110V router (e.g. Makita RTO700C).

For more information on spindles, please check out the Bill of Materials (BOM) [Link Here](https://github.com/RootCNC/Root_4_Lite/tree/main/BOM)

## Choice of Control Hardware/Firmware
Any solution that will drive at least 4 axes is theoretically suitable.  A robust and future-proof solution would be Pete’s own “Root Controller”, offering full opto-isolation and a multitude of driver and control options, Wifi operation and other benefits of ESP32 GRBL [FluidNC](https://github.com/bdring/Grbl_Esp32).  Beginners or those on a budget might consider an Arduino Uno or Mega solution with suitable shield (e.g. [RAMPS](https://reprap.org/wiki/RAMPS_1.4)).

## Choice of Box Section Rails
Aluminum box section is strong and light and won’t corrode.  Steel box section may need a little more cleaning, and if possible check the sizing with calipers before purchase.  Steel sections may be helpful for section lengths above 750mm.  Aluminum is fine otherwise.

## Hardware
If you’re not going to buy all the required parts straight away, consider at least ordering these parts first to allow assembly of the Y rails and X assembly:
- M5x60 pan head bolts (for the 8 carriages and 625 bearings)
	- M5 loc nuts
	- M5 washers
- M3x14mm cap head bolts
	- M3 nuts
	- M3 standard and penny washer
- Side panels
- Baseboard
- Box sections (aluminum or steel)
- Consider buying a set of bolts, washers and screws off Aliexpress or eBay initially
	-E.g. “1080pcs M2/M3/M4/M5 stainless steel bolts nuts screws heax head assorted”
	- (then buy specific items as needed afterwards)

## Tools
A set of extra-long Allen Keys with “ball ends” is recommended for R4L assembly.  Although not essential, these make some assembly steps (e.g. mounting steppers to motor mounts) much easier.

# Assembly

>General Notes:  The assembly guide below is a suggestion on how to proceed.   Steps may not necessarily have to be executed in the order shown, but others have found this a safe way to put the R4L together.
{.is-info}

## Baseboard Preparation
MDF or marine plywood are both suitable material.  It’s not essential to seal and paint the CNC sideboards or baseplate, but it may help avoid long term swelling from moisture, particularly if you will be using MDF.  

> MDF is particularly prone to absorption of both sealers and paint.  Consider applying at least 2 sealing coats before painting.
{.is-warning}

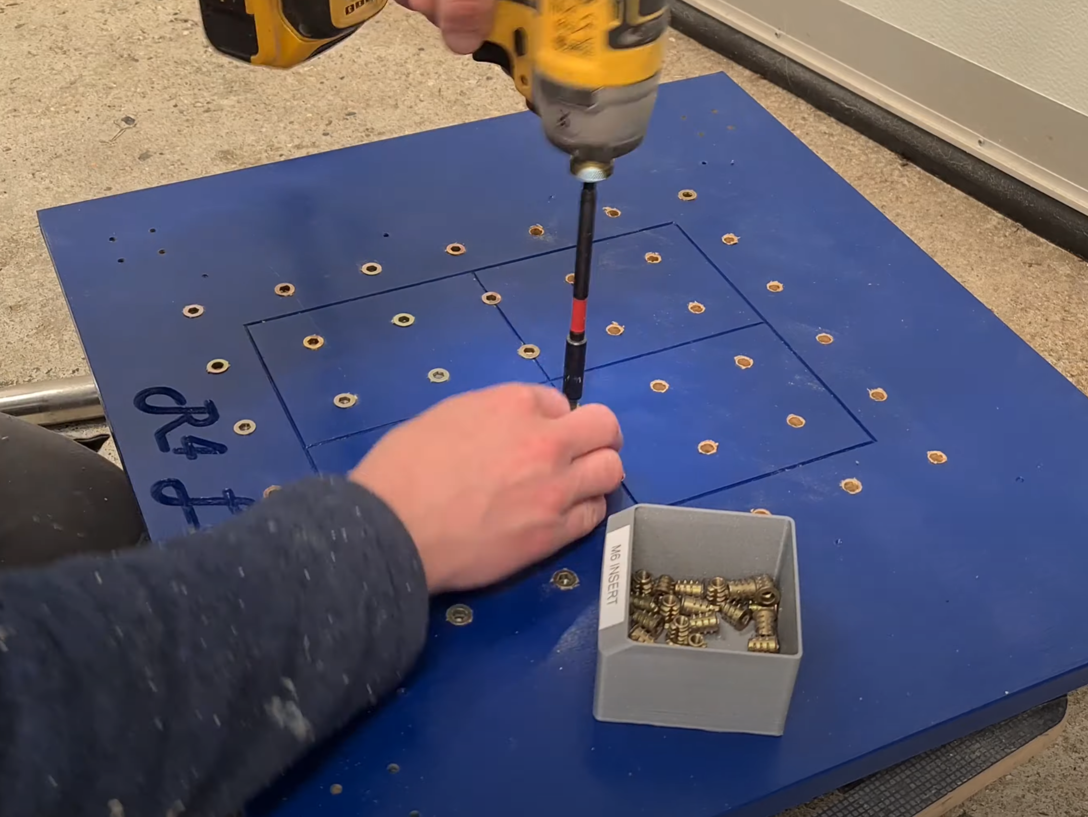
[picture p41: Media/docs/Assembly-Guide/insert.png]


It is easier to decide on any mounting hardware options before assembly, along with drilling holes and mounting inserts.

If you want to build a different size machine, there is a handly calculator to work out the size of the machine vs build area vs length of box sections: [LINK Working Area Spreadsheet](https://github.com/RootCNC/Root_4_Lite/blob/main/Working%20Area.xlsx)

There is also a handy tool to generate the a matrix of mounting holes within the baseboard, to aid in the mounting of work peices. This tool can be brought and downloaded from the store [Drill Location spreadsheet tool](https://rootcnc.com/product/drill-location-spreadsheet/)

#### Baseboard Video reference
- [R3L detailed build](https://youtu.be/z-iaeO7dcOc?t=655)  - 10:55 onwards
- [R4L Part one](https://youtu.be/DjvXqU2bEzY?t=469) 7:49 onwards)

## Carriages

Ensure any leftover support plastic inside the printed carriages is cleaned away.  A small allen key just large enough to clear the slot cut outs can help.  You may have more or less cleaning to do depending on how precise your 3D printer is creating the many internal cavities.  Gently run an M3 drill bit through the side holes to ensure the full depth is clear.
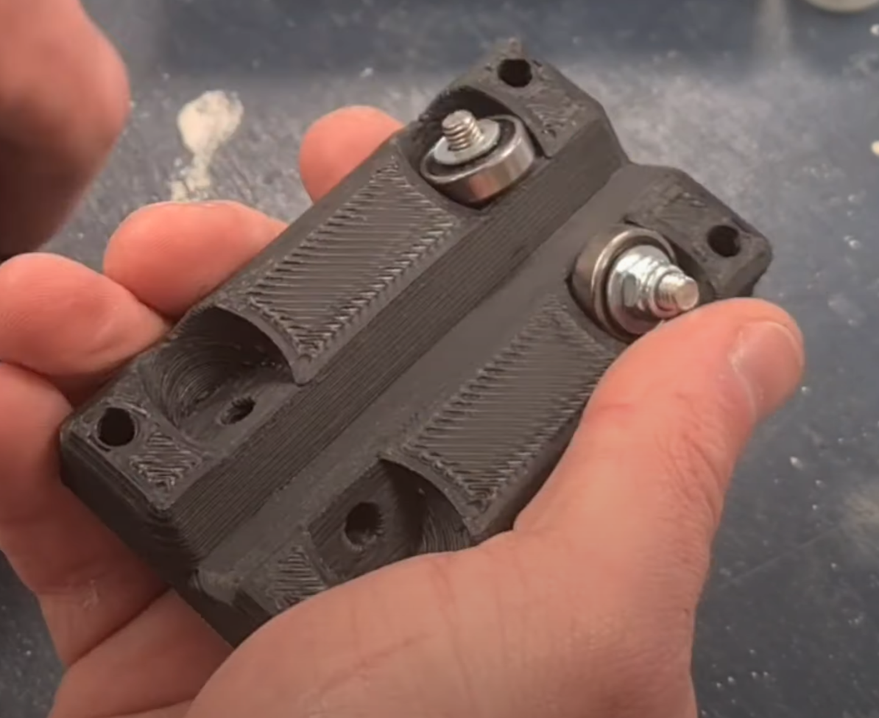
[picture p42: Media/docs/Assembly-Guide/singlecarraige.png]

Insert the M5x20 HEX head bolts (4 for each carriage plate), then locate an M5 washer, 625 bearing, 2nd M5 washer, and finally an M5 Loc nut.  Tighten nuts until just firm.

> Don’t assemble the carriage plates on the 20mm square box sections just yet.
{.is-info}

### Carriages Video reference
- [R4L Part one](https://youtu.be/DjvXqU2bEzY?t=489) 8:09 onwards

## Y Axis Sections
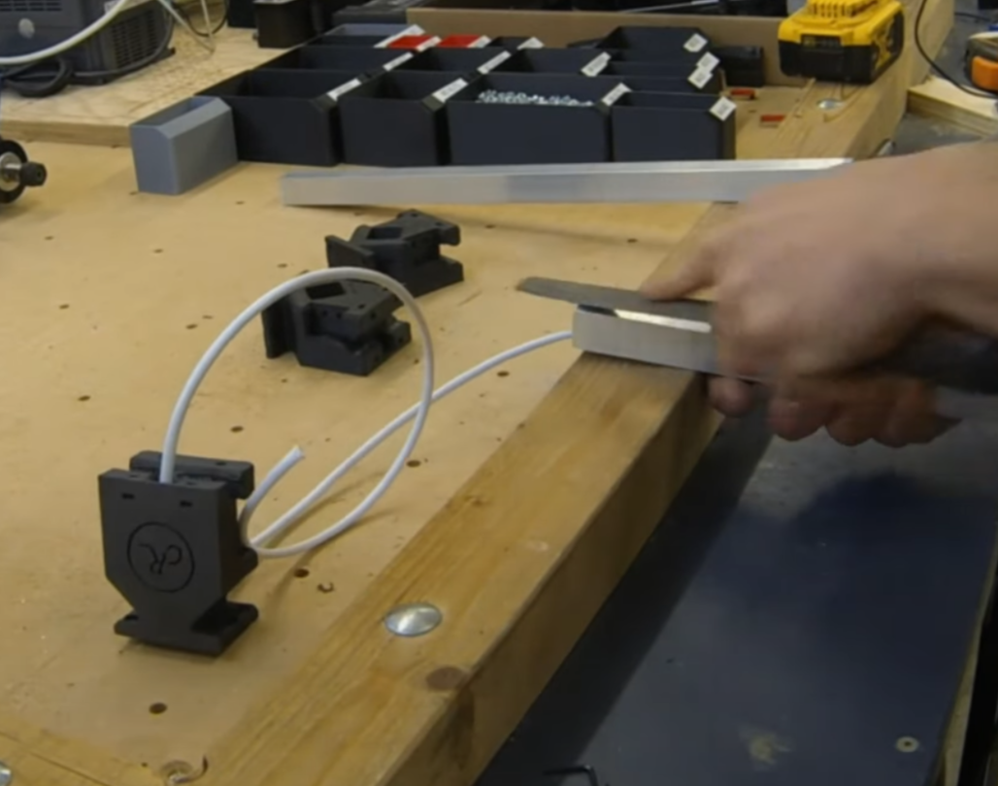
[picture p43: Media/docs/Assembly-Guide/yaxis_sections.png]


> Note If you intend to mount endstop switches at the front of the Y rails, or include wiring for future accessories, remember to run your shielded cable through the box section rails and Y axis boxmounts BEFORE assembly.
{.is-info}

Check the 4 box section lengths against the sizing spreadsheet for your planned build.  Make sure each end is filed slightly to take the off the edges and corners that will be inserted into the 3D printed Y Axis boxmount.  The Y axis rails will fit approx. 20mm inside each Y boxmount – do a pre-assembly check that the each rail with the 2 boxmounts attached will locate correctly on the baseboard holes.  Lightly mark each rail 20mm in from the end to ensure proper seating.  Using a mallet or wood block and hammer, knock the rail into each Y axis boxmount.  

Don’t mount the Y rails just yet – its best to assemble a carriage onto each rail before you mount rails to the baseboard.  
Video reference:  R4L Part two [Link](https://www.youtube.com/watch?v=-5PmiW85Cyw&t=618s) 8:47 onwards

## Y Rails and Carriages
Now assemble a pair of carriage plates on each Y rail.  Insert 4 M5x60mm Pan head bolts through the top carriage plate, an M5 washer and M5 nut on the other side, then the bottom carriage plate (on other side of the Y rail box section), then another M5 washer, and finally an M5 loc nut.  When all 4 M5x60 bolts are in place, gently but firmly tighten the loc nuts.  These need to be firm enough that the carriages sit firmly on the box sections with any rocking movement.  Slide the assembled carriage back and forth and check each of the 4x625 bearings is moving smoothly – if one or more aren’t rolling properly, then consider tightening the respective bolt a little more.  
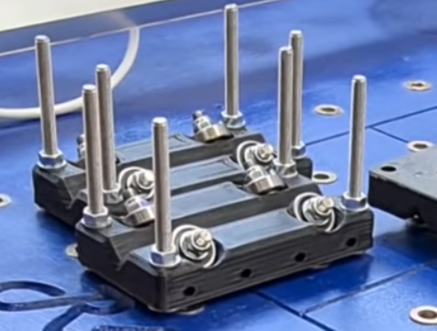
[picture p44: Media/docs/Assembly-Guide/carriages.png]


For the inward facing side of the carriages, it is worth seating M3 nuts in the various slots/cavities ready for later bolting to side panels and Z axis assembly.  To do this, pop an M3 nut into the top or bottom carriage slots.  Using an M3x30mm bolt, locate the nut onto the bolt, then tighten the bolt so the nut is pulled down into the hex-shaped cavity within the carriage.  It is particular helpful to do this for panel-facing sides of the carriages.  If any of the nuts don’t seat firmly, it might be helpful to put some masking tape over the nut slots to stop these escaping.

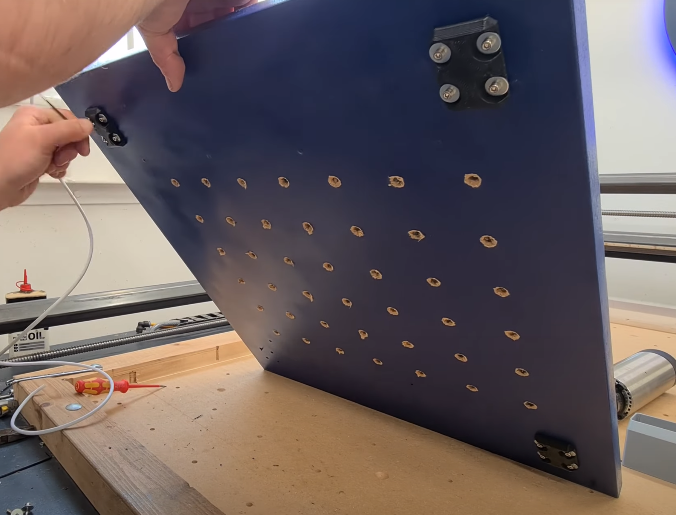
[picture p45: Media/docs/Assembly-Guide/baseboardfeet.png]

In a similar fashion, locate 4xM3 nuts in the front and rear slots near the base of each Y axis boxmount.  Locate the Y Axis boxmounts over the baseboard mounting holes.  Insert M3x30mm bolts from the bottom, located through a Y axis “foot”, up through the baseboard and up into the boxmount.  Gently tighten each M3 bolt with an allen key – consider inserting a small set of pliers into the boxmount slots to stop the M3 nuts popping out of their locating holes as the M3 bolts are tightened.  

Only loosely tighten each M3 bolt.  When both rail assemblies are mounted, check they are square on the baseboard and separated by the same distance at front and rear.  When positioned correctly, firmly tighten each M3 bolt from under the baseboard.   

### Y Rails and Carriages Video Reference
R4L Part three [Link](https://www.youtube.com/watch?v=_y3V89cwmr8) 7:22 onwards

## X Gantry Assembly
As per the Y rails, make sure there are no sharp corners or edges on each end of the X rails (box sections).  Using a mallet, gently knock each X rail into a single X-axis boxmount, making sure the completely flat outside surface of the boxmount is facing out from the box section rails.  Sit this out flat face on a block of wood when bumping in each X box section rail to ensure the end of the box section sits flush with the outside surface of the boxmount.  


### X Gantry Rails Video Reference
X Gantry Rails  R4L Part one [LINK](https://youtu.be/DjvXqU2bEzY?t=572) (9:30)

> Note that one end of the X-axis boxmount has a hollowed out space where the X axis endstops will eventually be mounted (circled in red).  This end will be pointing vertically UP.  
{.is-warning}

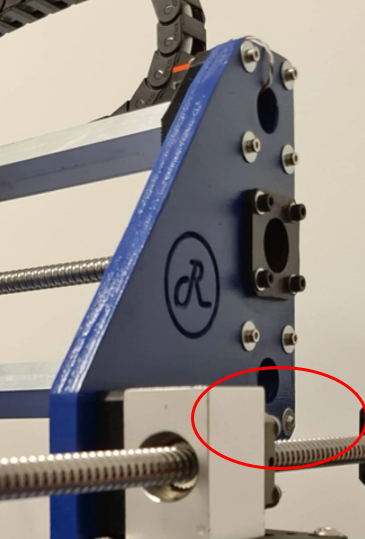
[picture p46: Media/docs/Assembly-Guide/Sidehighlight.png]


Now go ahead and mount the remaining 2 carriages on the X rails.  Just as you did for the Y rails, use M5x60mm Pan head bolts (bolt pointing downwards), M5 nuts, washers and loc nuts.  It’s worth using loc nuts on the bottom to ensure the correct mounting pressure on the rails - and also protect against spindle vibrations shaking these loose which will minimize the need for constant maintenance.  

Now is also a good time to drill and clean out the M3 holes on the gantry side facing the front of the machine and seat some M3 nuts in the carriage slots (again, same as previously done for the Y rails)

## Z Axis Linear Rail Mount Preparation
Drill/clean out the M3 holes for the linear rails and rear mounting holes on to the X gantry carriages.  Check the orientation of your linear rails before bolting them to the Z carriage – if at all possible you want to very top of the linear rail to be flush with the top of the Mount assembly (so that when we later mount an FK10 bearing block on the top of the linear rail mount it will be able to sit flat).  

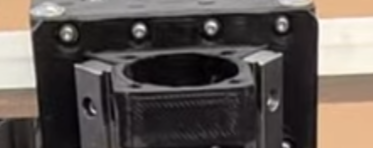
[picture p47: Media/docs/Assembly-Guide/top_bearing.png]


> The top of the linear rails should be flush with the very top of the linear rail mount assembly, or just below.
{.is-info}

Go ahead and mount the linear rails with M3x10 (or 8mm) bolts.  Slide the cars on to the linear rails.

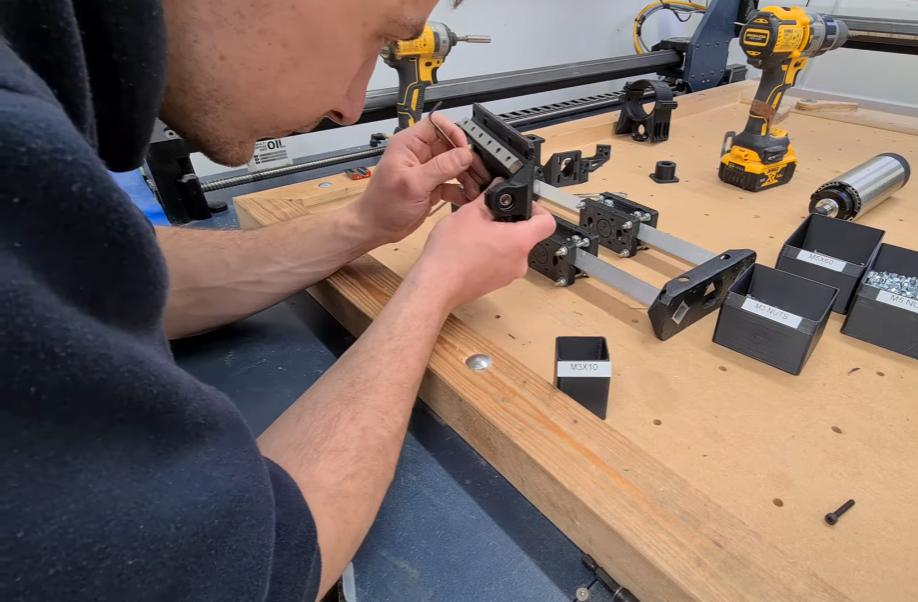
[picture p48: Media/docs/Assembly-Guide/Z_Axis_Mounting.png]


### Linear bearings Video Reference
Linear bearings being mounted R4L Part one [LINK](https://youtu.be/DjvXqU2bEzY?t=626) (10:26)

> Use 2 long bolts temporarily for the bottom most holes on the linear rails – to stop the cars sliding off the rails during later stages, until we eventually mount the Z axis carriage to these.
{.is-info}

## Mount the Z axis linear rail mount
Mount the Z axis linear rail mount to the X axis carriages.  Make sure you have the rail mount orientated right way up (Large FK10 bearing mount facing upwards).  Don’t be in a hurry to tighten down until all 16 bolts are seated loosely in their respective M3 nut, and the nut has retracted and seated into the carriage assembly so that it is held firmly and not rotating.  Once all bolts and nuts are seated and firm, then proceed to tighten everything up. Slide a 608 bearing into the bottom bearing mount of the linear rail mount – you shouldn’t have to squeeze too hard to get this in – consider running some sandpaper around the inside of the bearing mount to remove any rough plastic if the bearing doesn’t slide into please easily.

### Attaching linear rail mount Video Reference
Attaching linear rail mount to X axis carriages R4L Part one [LINK](https://youtu.be/DjvXqU2bEzY?t=711) (11:51)

## Mounting the X Axis gantry to the Y rails
Attach each panel to the carriages on the Y rails using M3 bolts and washers – you should have previously installed and seated the M3 nuts inside the carriages, but if you didn’t do so now.  Only loosely tighten each bolt, enough to ensure the corresponding M3 nut has retracted back into the carriage and not spinning.  You may need to use a small screwdriver or allen key on some of these to stop them spinning until they tighten down properly into the recess inside the carriage.

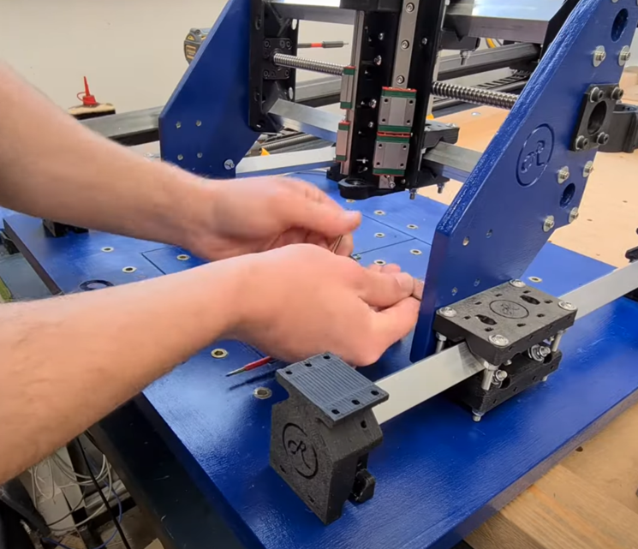
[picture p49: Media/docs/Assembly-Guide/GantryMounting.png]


### Attaching X gantry to Y rails Video Reference
Attaching X gantry to Y rails - R4L Part three [LINK](https://youtu.be/_y3V89cwmr8?t=331) (5:31)

Once all 16 bolts are in place, check the gantry is as close to vertical as possible, relative to the baseboard, using a large setsquare.  Take your time doing this, as it will result in properly square machine later on.  Check the X and Y rails are moving freely.  Tighten down the M3 bolts attaching the side panels to the Y rail carriages.   

If you left one Y rail only loosely tightened down on to the baseboard, now is the time to check again the Y rails are square and properly space to all the X gantry to slide smoothly fully forward and back.  Once satisfied, tighten down the M3 bolts to firmly lock into position this Y rail.  Don’t be too concerned if the machine isn’t perfectly square when the X gantry if fully forward or back – GRBL can autosquare out minor differences in the location of the Y rails and X gantry assemblies.   Check again the bolts on the X gantry and those attaching the sides panels are all firmly tightened.  

> Congratulations – you’ve now got something that’s starting to look like a CNC!  :)
{.is-info}



### Basic Motion Video Reference
End of R4L Part three [LINK](https://youtu.be/_y3V89cwmr8?t=331) (note Pete has already installed the X axis ballscrew in the pic)

# Motion Assemblies

Now it’s time to mount the stepper motor assemblies and get them wired in to your chosen driver/electronics solution.

## Y Axis Motor Assemblies
Select a Y Axis motor mount and look closely at how it will orientate on top of the rear Y Axis Box mount.  Note that the outside of one side in particular has a mounting to fit on to the box mount.  Also note the motor mount is not symmetrical – the box mount flanges are closer to one end of the motor mount – that is the end that will point away from the stepper motor.  Also think about the final orientation of your stepper motor wires – if you want these facing down towards the baseboard, make sure you take that into account when orientating and attaching your motor to the motor mount.

This is where extra long Allen keys will come in very handy.  Mount the motor to the motor mount with M3 bolts and washers.  I found some shorter M3x8mm bolts were handy here to make sure the bolts could be tightened down properly into the steppers.  Watch closely to make sure yours are tight with no “slop” once all 4 bolts are in place.

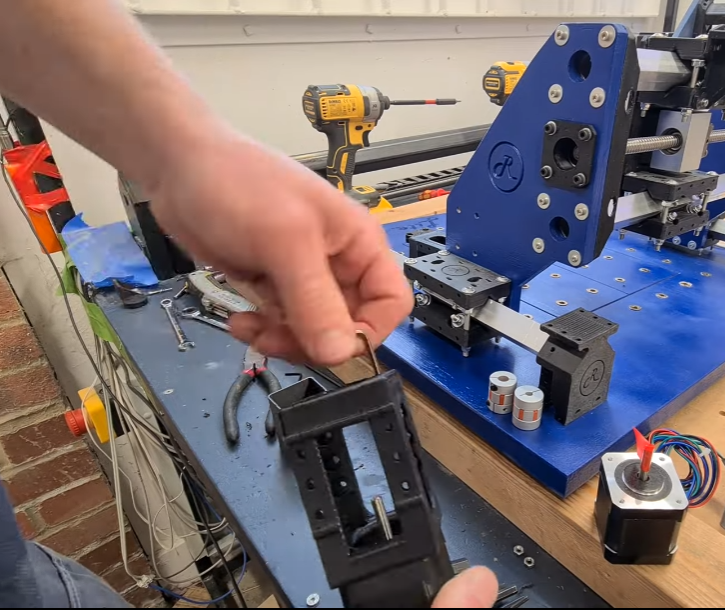
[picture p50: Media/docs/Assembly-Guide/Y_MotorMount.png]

### Video reference:
Y Axis motor assembly [R4L Part four](https://youtu.be/ivuQiyucW90?t=49) (0:49)

Slide a 5mm to 8mm coupler on to the stepper motor axle.  Next it’s time to mount your first ballscrew assembly.  Try to minimize how much you handle the screw.  New ballscrews come vacuum sealed from the factory and shouldn’t need lubrication, but you might want to attach one end to a hand-drill and run the ballscrew carriage from one end back to the other, then back to middle, to check nice smooth motion and straightness before installation onto the CNC.

Slide an FK10 bearing on to the 8mm axle of the ballscrew, also slide on the small bearing retainer nut (as per pic below) and tighten the grub screw.

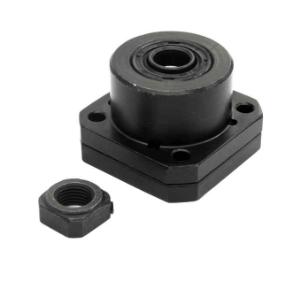
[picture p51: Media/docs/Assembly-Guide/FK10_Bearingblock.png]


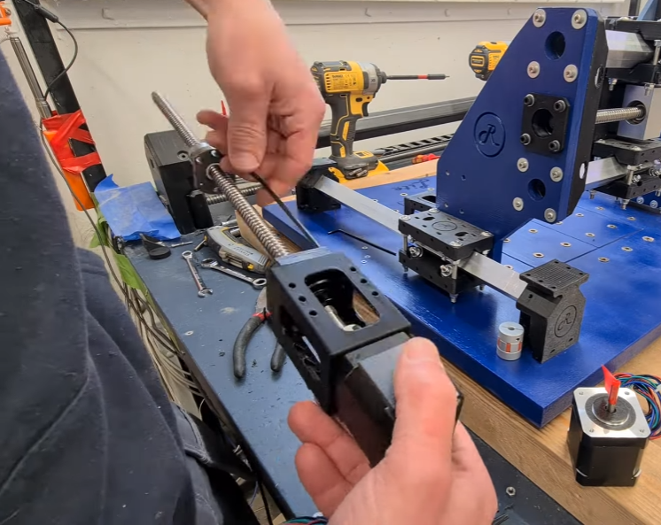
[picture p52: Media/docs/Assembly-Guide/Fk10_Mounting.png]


Attach the FK10 bearing to the motor mount with M4 bolts, washers and nuts.  Note the orientation of the ballscrew - check again yours is pointing in the correct direction ready to be connected to the aluminium ballscrew mount (on the X/Z gantry) later on.  To maximise the axis travel, you'll have to ensure the ballscrew nut is mounted  in the directions of Pete’s video, that’s how this guide will describe assembly.

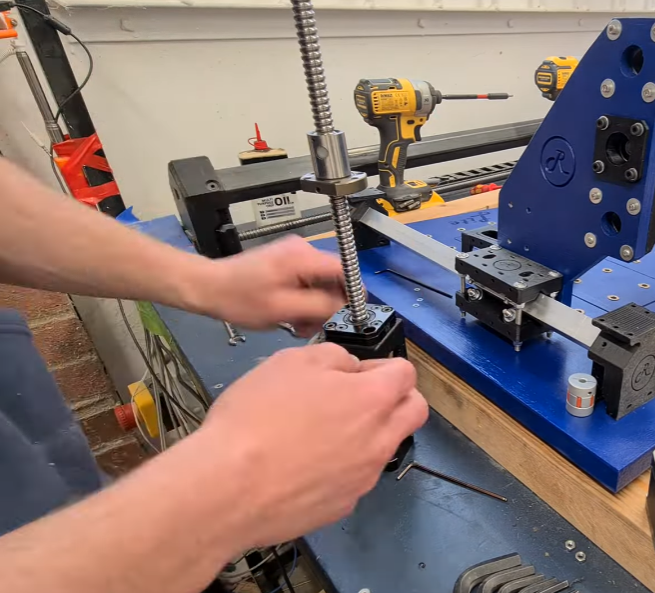
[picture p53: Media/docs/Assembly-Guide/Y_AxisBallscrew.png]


Install a 608 bearing into a Y axis idler and mount on top of each front Y axis box mount using M3 bolts, washers and screws.  Install the aluminium ballscrew mount on top of a Y rail carriage.  Make sure the mounting holes are pointing to the rear of the machine – attach to the side panel with M4 hardware.  Leave these mounting bolts slightly loose for now.

Slide the ballscrew through the aluminium housing mount and slot the front end into the 608 bearing idler.  Mount the Y motor housing down on the top of the rear Y axis boxmount using M3 hardware.

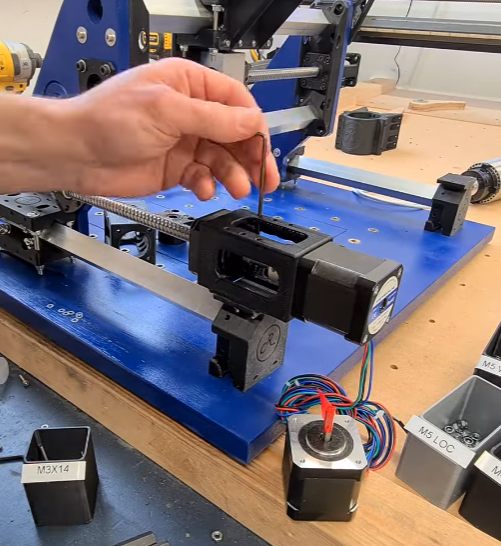
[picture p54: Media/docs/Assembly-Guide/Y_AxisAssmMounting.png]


Now manually turn the ballscrew so the carriage is snug inside the aluminum housing/mount.  Attach loosely with 6xM4 bolts and washers.

You should now have an entire Y axis motor assembly, loosely mounted.  Check the ballscrew can turn freely, then gradually tighten down all the mounting hardware.  Suggested order:
- Check the Idler mount on the front Y Axis boxmount is bolted down tightly and the bearing is seated correctly
- Tight the M4 bolts connecting the ballscrew carriage to the aluminium mount block
- Tighten the M4 hardware attaching the aluminium ballscrew housing/mount to the side panel
- Check the Y motor mount is tightly bolted down on top of its Y axis boxmount
- Check the FK10 bearing tensioner grub screw is tight
- Now tighten both sides of the 5mm to 8mm coupler connecting the stepper motor axle to the ballscrew axle.  

When all of this is done you should be able to gently turn the ballscrew by hand and feel the X gantry moving smoothly forwards and backwards (as you manually move the opposite side of the gantry) without binding.  If you do have binding, then consider loosening all the fittings and retaining bolts and trying again.

Now, repeat all these steps for the 2nd Y axis motor assembly.  Take your time and double check the orientation of the motor on the motor mount so the stepper motor wires are pointing where you want them to go.  Don’t be in a hurry to tighten down hardware until the end, to help ensure everything is aligned and able to move freely before we start powering up motors later on.

 # X Axis Motor Assembly

Armed with your new knowledge of ballscrews and motor mounts, now is a good time to install the X axis ballscrew and motor assembly.  Pete does this in the 2nd assembly video, but makes some suggestions on how to do this in the easiest most efficient fashion, which we’ll try to take advantage of.

First install the X axis bearing idler on the right side of the gantry using M4 hardware.  Next mount the X axis stepper motor on to its Motor Mount with M3 hardware, and slide on a coupler.  The FK10 bearing on the left side of the gantry sits inside the left panel.  The M4 mounting bolts will need to be long enough to fit through the bearing, side panel and into the motor mount on the other side.  Slide the ballscrew into place in the aluminium housing mount and insert loosely into the FK10 bearing.  Make sure you also slide the bearing retaining nut on to the ballscrew axle inside the motor mount.

Now it’s time to tighten the M4 hardware connecting the motor mount and FK10 bearing.  Tighten the bearing retainer grub screw.  Slide a 608 bearing into the bearing idler on the right side of the machine and install an 8mm circlip to hold the bearing in place.

Attach the ballscrew carriage to the aluminum mounting block (on the rear of the Z carriage) with 6xM4 hardware – don’t tighten these fully just yet.  With the X axis motor and ballscrew assembly in place check the ballscrew can be turned manually with no binding.  Once satisfied everything is ok, it’s time to tighten down.  Suggested order:
-First tighten the 6xM4 bolts attaching the ballscrew to the aluminium housing mount
-	Then tighten the M4 bolts attaching the aluminium mount to the Z axis linear rail mount
-	Check the FK10 bearing and motor mount M4 bolts are tight, and the M3 bolts attaching the X axis stepper are tight
-	Check the ballscrew bearing retaining nut grub screw is tight
-	Finally tighten down the 5mm to 8mm coupler connecting the stepper motor axle to the ballscrew
-	
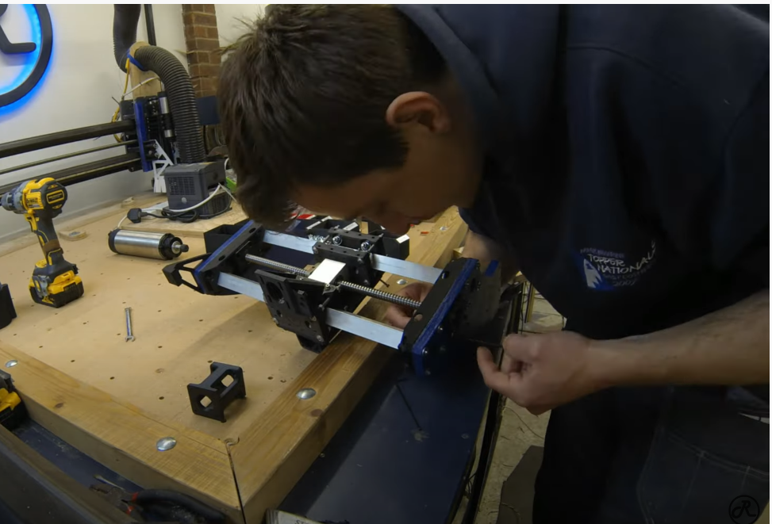
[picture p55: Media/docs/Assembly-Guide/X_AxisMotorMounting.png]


## Video reference
Pete assembly X axis ballscrew assembly [R4L Part two](https://youtu.be/-5PmiW85Cyw?t=331) (5:30)

# Drag chain mounts

Attach the Y axis drag chain mount to the left Y axis carriage with M3 hardware.  Install your chosen cabling into both dragchains, then connect both drag mounts to the Y and X axes with M3 hardware.  You’ll need to shorten your drag chain accordingly to the size of your build.  

Note:  Make sure you have plenty of cable length to reach the Z carriage assembly – read through the Z carriage installation below first to be double-sure about this.  Where in doubt, make the cables a bit longer than required between the motors/endstops and the control board connections.

> Note:  Make sure you have plenty of cable length to reach the Z carriage assembly – read through the Z carriage installation below first to be double-sure about this.  Where in doubt, make the cables a bit longer than required between the motors/endstops and the control board connections.
{.is-success}

# Z Carriage Wiring Preparation
High quality shielded multi-core cable is recommended for endstop and motor wiring to minimize electrical interference with your movement signalling.  Remove the outer cable shielding from the Z axis endstop wires.  Twist approx. 20cm of exposed wires into a pair – Pete does this quite neatly using using a handrill.  Take a photo of your wiring pairs so you can remember which colours are paired for which sensor when you later wire up the control board.  

Ensure the Z carriages are clear of any stray plastic – drill out mounting holes gently and make sure the wiring cavities are clear by inserting a test wire.  

Insert both wire pairs through the Z carriage, one pair each for the top and bottom endstop sensors:

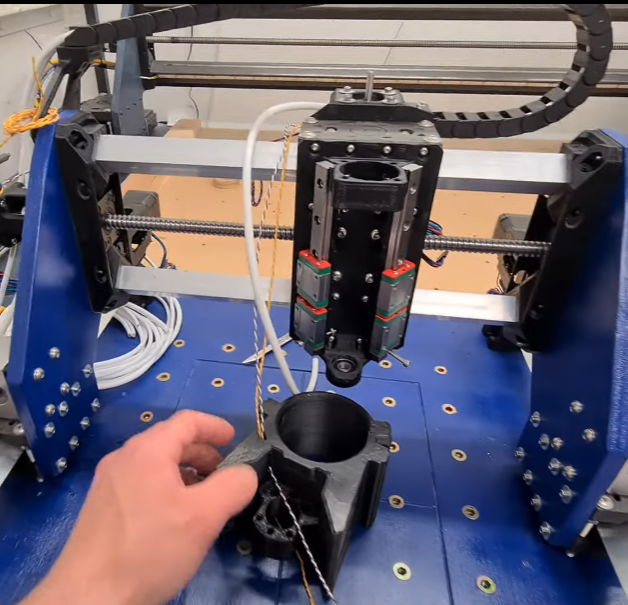
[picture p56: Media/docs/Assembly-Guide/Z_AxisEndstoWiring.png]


# Z Carriage Endstop Wiring

A full description of wiring options is beyond the scope of this assembly guide.  The reader is advised to avail themselves of Pete’s wiring info on the Wiki, and give some thought as whether you will be configuring your endstops as “normally closed” (NC) or “normally open” (NO), and possibly also if they will be set up serial or parallel.  Both NC and NO have advantages and disadvantages in terms of safety, ease of configuration, etc.  It is recommended you do some test wiring and connection to your chosen control board and software ecosystem before wiring up the Z carriage to make you know which connectors you will be using on the endstop switches, if your control board responds correctly to your chosen NC/NO configuration, etc.

> The Z carriage area is a very tight working environment.  It was elegantly designed to fit as much hardware functionality as possible into a small space, and with minimal X width (to maximize the working width of your CNC in the X axis).  The trade off is assembly at this point is tight and a bit tricky -  so take work carefully and check assembly at each step.
 {.is-info}

Try to anticipate the length of endstop wires you need to have no tight spots, but also not excessive loops that risk getting caught.  Cut each pair to the chosen length.  Slide a short length of appropriate sized shrink wrap over the wire pair, then solder each wire to the appropriate sensor terminals.  Slide the shrink wrap over the connection and apply heat to protect the connection.

Loosely attach each endstop in its final position with appropriate small bolts, making sure the wire pairs are safely routed back into the carriage.

Install the Z axis ballscrew, attaching the ballscrew carriage down into the Z carriage with M4 hardware.  Consider avoiding washers for the bolts closest to the X rails - to avoid any protrusions  that might rub against the assembled Z axis linear rail mount.  Leave the M4 bolts only loosely tight for now.  Once the ballscrew is in place, tighten up the bolts on the endstops.



# Installing the Z Carriage

Slot the bottom of the Z ballscrew into the lower 608 bearing with the top of the axle protruding through the FK10 bearing mount.  Connect the FK10 bearing with M4 hardware, and install the bearing retaining nut on top.  

> The nuts for the M4 bolts attaching this top FK10 bearing are seated inside the top of the linear rail assembly and may be tricky to keep in place (without falling down into the insides of your Z carriage assembly).  It is worthwhile seating these before you actually insert and attach the bearing block – install the nut and washer underneath and gently tighten an M4 bolt from the top until the M4 nut pulls up into the linear rail assembly and is seated firmly.  When it is time to later install the FK10 bearing, very carefully install the M4 bolts so you don’t knock out these pre-seated M4 nuts.  It may also help to use some “Blu-tack” behind the M4 nuts to further reduce the chance of these nut falling down during bear assembly.
 {.is-info}

Next loosely fit the 16xM3 bolts on each side of the Z carriage through into the linear rail blocks.  Make sure these are the right length so you can tighten them down firmly at the end (e.g. consider having some M3x8mm bolts on hand if M3x10 is too long for your rail block threads).

Manually run the Z axis ballscrew back and forth through its full reach of movement checking for any binding.  The two extra long M3 bolts we used at the bottom of the linear rail can be replaced with their correct final shorter size now.   Suggested order for tightening down Z axis hardware:

-	M3 bolts connecting Z carriage to rail carriages
-	Tightening of M4 bolts on FK10 bearing 
-	Grub screw on top FK10 bearing nut retainer
-	Final tightening of M4 bolts connecting ballscrew carriage to Z carriage

Don’t rush these steps – if the Z axis ballscrew isn’t turning freely you risk losing motor steps or belt control during operation of the Z axis.  If you can’t turn the ball screw smoothly and easily, repeat the process to try again.   

Install the Z axis motor with M3 hardware.  Connect the appropriate bore pulley gear to both the Z axis motor and top of the Z axis ballscrew.  Install the belt, and adjust the location of the Z motor such that the belt is firm and tight.  Tighten Z motor hardware in position.  

Install the four accessory rail knurled nuts on the Z carriage, along with the 4xM3 bolts for tightening the spindle mount.  Check the spindle/router can be installed and held in place straight and firm.  You may need to shim the router inside the Z carriage later on to ensure it is properly square with the machine and baseplate.  Manually move the Z axis through its full range of motion and again check nothing is binding or rubbing.  

# Install Remaining Wiring

As per Pete’s wiring guide, connect the X, Y and Z axis motors to your control board.  Thread cabling through the X gantry and wire up the Min and Max X axis endstops (again, according to your chosen method of NO, NC operation).  Install and wire the Y axis endstops, running and attaching cabling under the baseboard as required.  
Wire up your spindle with fully shielded cable.   If you are using a router instead of a spindle, consider using cable ties to safely route the power lead back along the X axis gantry and off the side of the machine.  

# Final wiring and commissioning tests

CNC newbies will still have lots to learn about CAD, CAM and gcode sending software, wasteboard installation and how to clamp your work.  The journey has only just begun .  For your very first motion tests consider attaching a felt pen to the Z carriage and checking you have free and reliable motion of all axes sufficient to draw an appropriately scaled SVG vector graphic.  

Please share your build experience and photos on the Root Discord, and don’t be afraid to suggest improvements to the Root CNC Wiki.  

Finally, locate a **cold beer** and **sit back** to celebrate and survey your fully operational Death Star, Root 4 Lite CNC.  :smiley:



> Massive thank you for Robs contribution to the wiki! 
{.is-success}

# Support the Wiki!
If you would like to support the project and provide information on specific machines, then please check this [page out first](https://wiki.rootcnc.com/en/Root-CNC/Contribute). Failing that, please let me know which area you want to contribute to and I can add your information to help others out!

# Social links
 1. [Facebook Group](https://www.facebook.com/groups/rootcnc/) 
 2. [Discourse](https://rootcnc.discourse.group/) 
 3. [Discord](https://discord.gg/93Ue5SwthW) Great for quick answer to questions
 4. [Thingiverse](https://www.thingiverse.com/sailorpete/designs) 
 5. [Youtube](https://www.youtube.com/c/sailorpete12/)

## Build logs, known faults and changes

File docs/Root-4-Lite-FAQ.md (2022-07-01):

---
title: Root 4 Lite FAQ
description: Root 4 Lite FAQ for Newbies
published: true
date: 2022-06-28T21:37:30.411Z
tags: root 4 lite, r4 lite, guide
editor: markdown
dateCreated: 2022-05-24T19:30:47.756Z
---

#Root 4 Lite FAQ</strong>

#Is Root 4 Lite suitable for my needs?

#How large should I build?

#How do I go about 3D printing the parts?

#What materials will I &nbsp;need?

#How to I get a suitable base board and side panels?

#What tools are required?

#What will it cost?

#What spindle should I use?

#What controller, drivers, &nbsp;and power supply should I use?

#What skills will I need?

#What if I get Stuck?

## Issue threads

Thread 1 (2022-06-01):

DustShoe_Rail_Left.STL missing

jamesagarside, 2022-06-01:
The STL for DustShoe_Rail_Left is not contained within this repo.

tiberiuichim, 2023-04-09:
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
https://wiki.rootcnc.com/en/Root-4-Lite/Print-Info

Closed 2023-08-11.

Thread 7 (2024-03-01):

Link on Wiki points to folder changed by a commit

apopanda, 2024-03-01:
https://github.com/RootCNC/Root_4_Lite/commit/43c43693bef340b010f34be5502c8a913ad595eb
The change here broke links in the Wiki.
Specifically: https://wiki.rootcnc.com/en/Root-4-Lite/Assembly-Guide
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

apopanda, 2024-03-01:
Also here
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

SnowB0und14, 2024-04-04:
I noticed this as well.  I found the links on the actual Root 4 GitHub.

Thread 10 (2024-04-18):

X_Axis_BoxMount M3 wrong nut size

anjoze, 2024-04-18:
The M3 nuts on X_Axis_BoxMount.STL are loose. I thought it was a chinese nuts problem but when I measure the holes  of X_Axis_BoxMount.STL on Prusa slicer its 3.580mm.
Comparing it with Z_Axis_LinearRailMount M3 nuts (3.464mm), I see that they are bigger.
That difference make the X_Axis_BoxMount install process really difficult because the nuts are always spinning

This was discussed here:
https://discord.com/channels/795012056943296522/846512530004246558/1227605058942668851

SnowB0und14, 2024-04-24:
I re worked that part and created a pull request for it.  You should be able to find an updated file if you look there.

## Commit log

2021-04-29 Added STL Files
    [DustShoe_Bottom.STL, DustShoe_Rail_Right.STL, X_Aixs_DragChainMount.STL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]
2021-05-06 Added DXF Parts
    [Root_4_Lite_Side_Panel_(Back).DXF, Root_4_Lite_Side_Panel_(Front).DXF]
2021-05-17 BOM added
2021-09-23 Create Working Area.xlsx
    [Working Area.xlsx]
2022-02-15 Minor Update
    [Working Area.xlsx]
2022-07-01 Update Print Info.md
2022-08-17 Update Assembly-Guide.md
    fixed minor formatting errors
2022-09-14 moved print info media to their own folder
2022-09-14 moved assembly guide media to their own folder
2023-06-09 Added Laser mount files
    [Z_AxisMount.STL, Z_AxisMountBottom.stl, Z_AxisMountTop.stl]
